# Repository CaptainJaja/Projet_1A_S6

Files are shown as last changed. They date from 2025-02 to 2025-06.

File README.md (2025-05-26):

# 🚀 Projet 1A S6 - Robot Bluetooth + Odometrie

Ce projet consiste à concevoir un robot télécommandé via Bluetooth grâce à une application Android, avec odométrie, détection d'obstacles, et supervision ROS.

---

## 📌 Cahier des charges

### 🔹 Robot
- Communication **UART** avec le module **Bluetooth HC-05**  
- **Contrôle de deux moteurs DC à encodeurs** via un driver **TB6612FNG**  
- **Lecture des encodeurs** pour faire de l'**odométrie**  
- **Connexion à une Raspberry Pi** pour supervision et traitement via **ROS**  
- **Détection d'obstacle** via un capteur **ultrason HC-SR04**  
- **Module infrarouge** pour détection de ligne ou d'obstacles courts  
- **Affichage LED** pour état du robot ou esthétique  
- **Commande de deux servo-moteurs** pour actionner des éléments  

### 🔹 Application Android
- Interface graphique avec **boutons de commande**  
- **Connexion Bluetooth** pour envoyer des commandes au robot  

---

## ⚙️ Matériel utilisé

| Composant | Référence | Rôle |
|---|---|---|
| **Microcontrôleur** | STM32 (modèle à préciser) | Gestion des moteurs, capteurs, servo et communication Bluetooth |
| **Module Bluetooth** | HC-06 / HC-05 | Communication avec l’application Android |
| **Moteurs DC à encodeur** | GA12-N20 + encodeur magnétique | Déplacement du robot + odométrie |
| **Driver moteur** | TB6612FNG | Pilotage des moteurs |
| **Batterie** | LiPo 7.4V (capacité à préciser) | Alimentation du système |
| **Régulateurs de tension** | 7.4V → 5V (R-78B5.0-2.0), 5V → 3.3V (BU33SD5WG-TR)| Alimentation des composants |
| **Capteur ultrason** | HC-SR04 | Détection d'obstacles |
| **Module infrarouge** | (modèle à préciser) | Détection de ligne ou d'obstacle proche |
| **Servomoteurs** | (modèle à préciser) x2 | Actionneurs divers |
| **LEDs** | 2x minimum | Indicateurs visuels |
| **Raspberry Pi** | (modèle à préciser) | Exécution de ROS et traitement haut niveau |

---

## 🛠 Architecture du PCB

Notre projet comporte **deux versions de PCB** :

### V1 : Prototype de base
- Connecteurs moteurs, servo, HC-SR04, HC-05 ; Driver ; STM
- Pas d'encodeur, ni module infrarouge, ni connecteurs pour la Raspberry Pi

### V2 : Version finale
- Connecteurs pour les **encodeurs**, la **Raspberry Pi**, et le **module infrarouge** ajoutés
- Circuits d'alimentation optimisés pour alimentation partagée

---

## ⏳ Tableau d'avancement du projet

| Séance | Avancement |
|---|---|
| Séance 1 | Répartition des tâches (modélisation 3D / code + PCB / appli Android), choix des composants |
| Séance 2 | - Début du PCB V1 (sans encodeur, Raspberry, infrarouge) <br>- Début application Android <br>- Début modélisation mécanique |
| Séance 3 | - Finalisation du PCB V1 <br>- 1ère version de l'application (nombreuses fonctionnalités manquantes)<br>-la conception 3D continue d'avancer |
| Séance 4 | - Début des tests du **module HC-05** <br>- Implémentation des fonctionnalités mais beaucoup d'erreurs <br>-changement des dimensions de la structure 3D car changement d'agencement des éléments dans le robot |
| Séance 5 | Finalisation de la **commande à distance** (prototype robot avec HC-05)<br>-la conception 3D continue d'avancer |
| Séance 6 | - Début du PCB V2 (ajout Raspberry, encodeurs, infrarouge) <br>- Plus d'erreurs grâce aux bonnes permissions demandées <br>- début de l'impression 3D |
| Séance 7 | Finalisation du modèle du PCB V2, **commande des composants et du PCB** <br>-fin de l'impression 3D |
| Séance 8 | Finalisation du modèle 3D, montage PCB et robot prototype, test |
| Séance 9 | Corrections et impressions 3D, montage du robot final |
---

## 📋 Répartition des tâches

| Nom | Tâche principale |
|---|---|
| **CAPODAGI Janus** | Conception PCB (https://github.com/CaptainJaja/Projet_1A_S6/tree/main/Hardware/PCB),  code STM32 (https://github.com/CaptainJaja/Projet_1A_S6/tree/main/Software/Code) |
| **BUI HAI Christophe** | Développement de l’application Android (https://github.com/CaptainJaja/Projet_1A_S6/tree/main/Application) |
| **MILLON Raphaëlle** | Conception mécanique du robot :modélisation 3D, intégration Raspberry (https://github.com/CaptainJaja/Projet_1A_S6/tree/main/Hardware/3D) |

---

## 📝 Remarques et pistes d'amélioration

- Ajouter un schéma de l'architecture du système (STM32 + Raspberry + ROS)
- Tester la communication entre STM32 et Raspberry via UART 

---

Ce README est susceptible d'être mis à jour au fur et à mesure de l'avancement du projet. 🚀

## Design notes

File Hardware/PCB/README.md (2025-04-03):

# 🚀 Robot PCB - STM32 + HC-05 + Motor Driver  

Ce projet est un PCB conçu pour contrôler un robot suiveur de ligne avec obstacle, utilisant un **STM32L552CCTx** et un module **Bluetooth HC-05** pour la communication. Il comprend un **driver moteur TB6612FNG**, plusieurs GPIO et connecteurs pour capteurs.

## 📸 Aperçu du PCB version 1 (moteur sans encodeur, pas de connexion raspberry)
### **Face Avant**
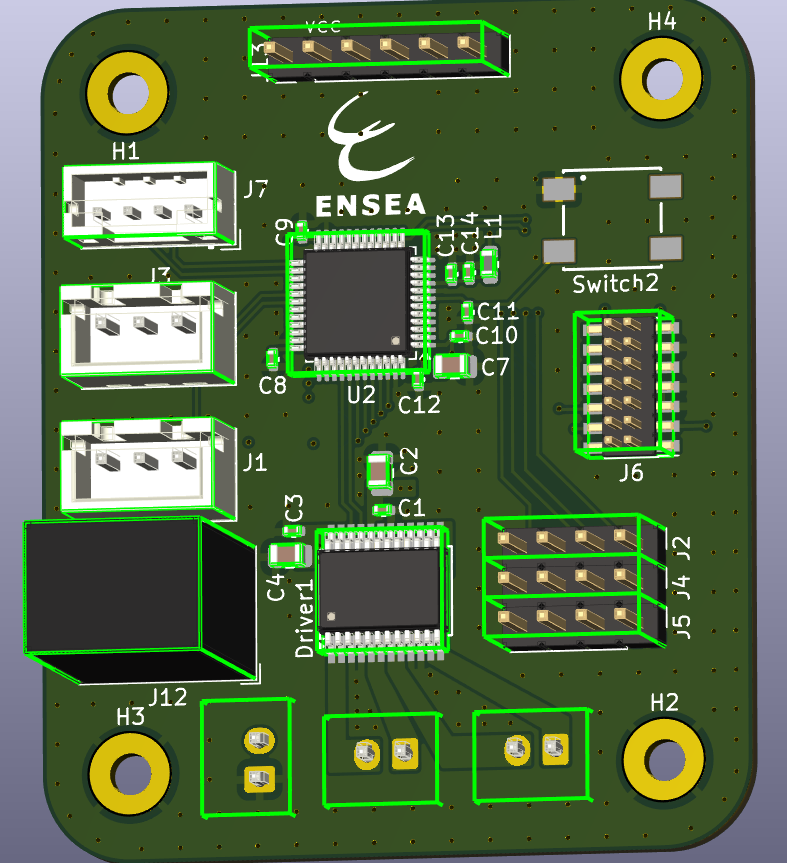
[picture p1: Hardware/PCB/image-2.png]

### **Face Arrière**
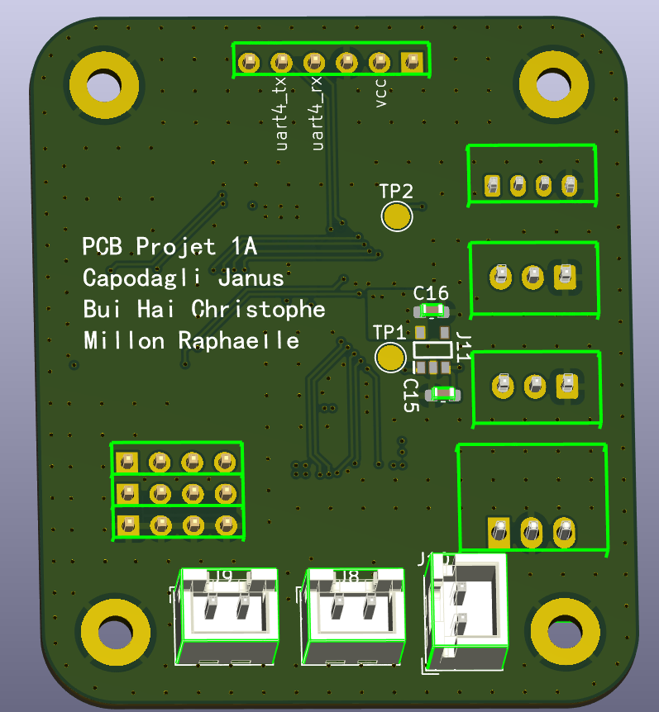
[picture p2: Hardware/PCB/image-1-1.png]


## 📸 Aperçu du PCB version 2 (+moteur avec encodeur, +connexion raspberry (UART), +Module infrarouge)
### **Face Avant**
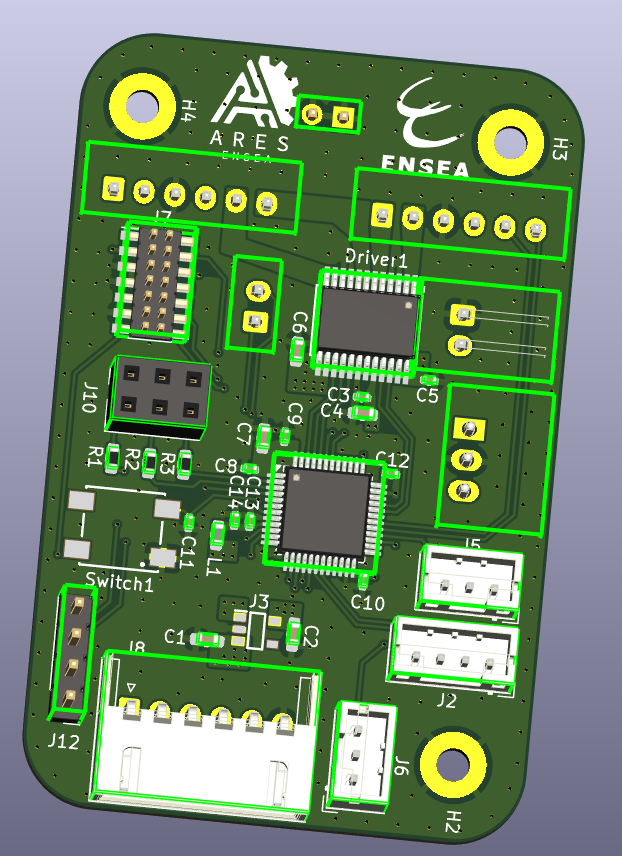
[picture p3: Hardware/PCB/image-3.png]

### **Face Arrière**
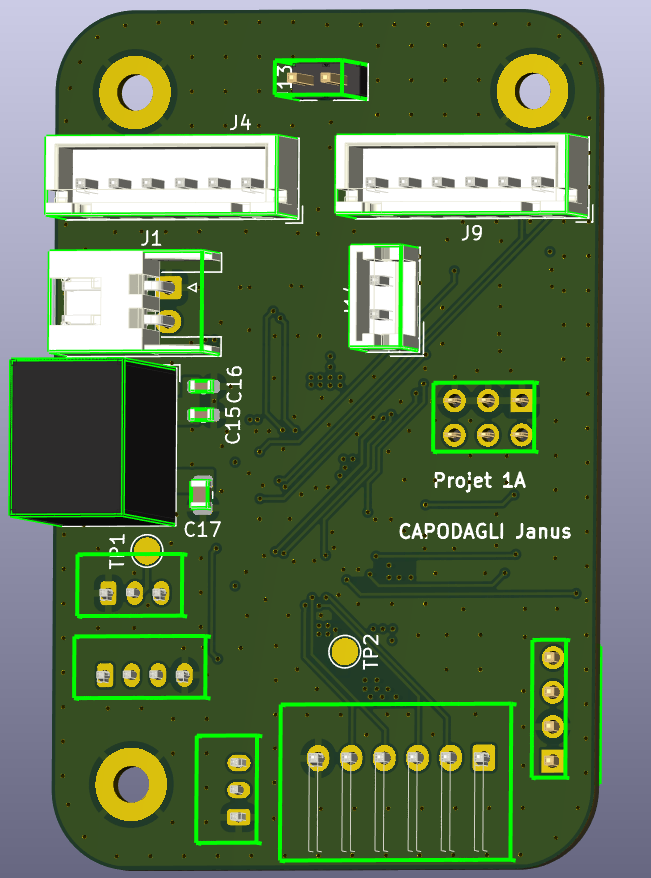
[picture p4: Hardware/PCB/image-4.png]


## 📦 Composants intégrés (version finale : V2)
- **Microcontrôleur :** STM32L552CCTx
- **Communication (PinHeader 01x04) :** HC-05 (Bluetooth, connecté en UART au MCU)
- **Contrôle des moteurs :** TB6612FNG (Driver moteur DC)
- **Indicateur d'état Bluetooth :** LED
- **Interface GPIO :** Rangée **3x4 pinheader** (GPIO-3.3V-GND)
- **Connectique :**
  - 2x **Connecteurs JST 01x03** pour servomoteurs
  - 2x **Connecteurs JST 01x06** pour moteurs DC
  - 1x **Connecteur JST 01x06** pour module infrarouge
  - 1x **Connecteur JST 01x02** pour alimentation
  - 1x **Connecteur ST-LINK** pour programmation/debug
  - 1x **Connecteur PinHeader 01x02** pour connexion UART avec raspberry
  - 1x **Connecteur PinHeader 02x03** pour connexion avec les LEDs
  - 1x **Connecteur PinHeader 01x02** pour connecter les masses STM/Raspberry
- **Alimentation :**
  - **Régulateur 7.5V → 5V**
  - **Régulateur 5V → 3.3V**
- **Boutons poussoirs :**
  - **Reset du MCU**
- **Passifs :** Condensateurs de découplage, bobine, résistances (**SMD**)

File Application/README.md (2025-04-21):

# Contrôle d'une Voiture Télécommandée via Bluetooth

## Introduction

Nous souhaitons programmer une application sur **Android Studio** afin de contrôler une voiture télécommandée via **Bluetooth** depuis un smartphone.

---

## Difficultés

- **Android Studio** utilise trois langages de programmation : **Kotlin, Java et XML**.
- Les fichiers présents sur GitHub contiennent un programme en **Kotlin** permettant d’établir une connexion Bluetooth.
- Cependant, ce programme comporte des **erreurs** que je n’arrive pas à corriger (ne connaissant pas Kotlin).
- Par conséquent, j’ai décidé de configurer **Android Studio** pour ne programmer qu’en **Java**.

---

## Mise en place du code Java

Sur un **nouveau projet vierge** :

### 1️⃣ Remplacement du fichier MainActivity
📂 **Chemin du fichier :**  
`D:\Projets\Formation_Android_Studio\app\src\main\java\com\example\formation`

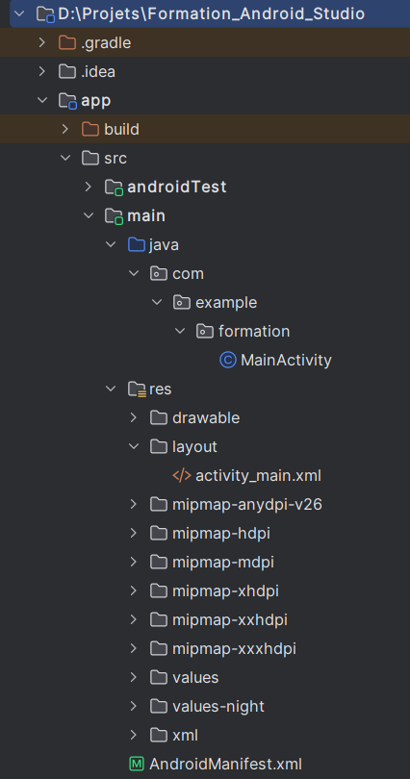
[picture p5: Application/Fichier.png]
Fichier


✅ **Modification :**  
- Remplacement du fichier **MainActivity.kt** par une classe **Java**.

### 2️⃣ Modification du fichier activity_main.xml
📂 **Chemin du fichier :**  
`D:\Projets\Formation_Android_Studio\app\src\main\res\layout\activity_main.xml`

🖼️ **Objectif :**  
- Ajuster automatiquement l’interface utilisateur aux dimensions de l’appareil.
- Le fichier `activity_main.xml` gère la **mise en page de l’application**.

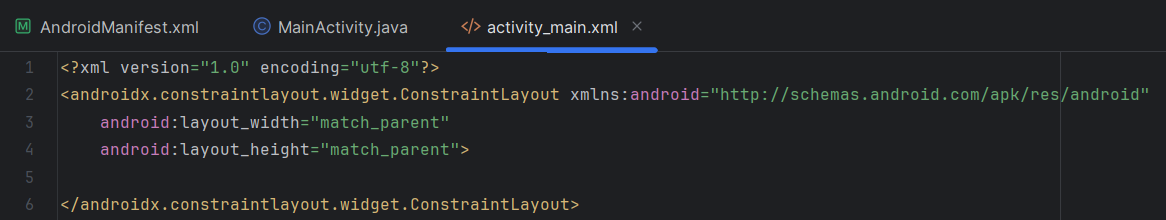
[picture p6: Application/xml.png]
activity_main.xml


### 3️⃣ Configuration du fichier AndroidManifest.xml
📂 **Chemin du fichier :**  
`D:\Projets\Formation_Android_Studio\app\src\main\AndroidManifest.xml`

✅ **Modifications :**  
- Déclaration de **MainActivity** comme **activité principale** de l’application.

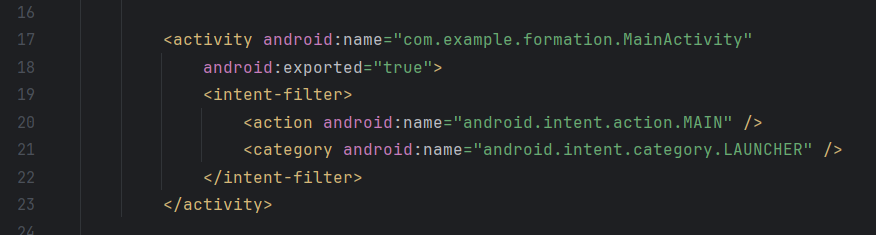
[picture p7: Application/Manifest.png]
AndroidManifest.xml


---

## Travail à faire ✅

🔹 **Se familiariser** avec **Android Studio**  
🔹 **Implémenter** le programme de **connexion Bluetooth en Java**  

---

# Séance du 06/03/2025

On en est à la version 1 du programme. Or il comporte des lacunes :

- Le programme nécessite dans le code l'adresse MAC du module Bluetooth. Dans l'idéal, on aimerait pouvoir se connecter depuis l'application à partir d'une liste d'appareils.
- Le module nécessite un PIN : le programme n'est pas adapté pour cela.
- On ne l'a pas testé car il y avait des problèmes de connexion avec le module.

On va donc en attendant essayer d'implémenter ces fonctionnalités.

---

# Séance du 13/03/2025

En modifiant le programme, j'arrive à avoir une interface sur mon portable :

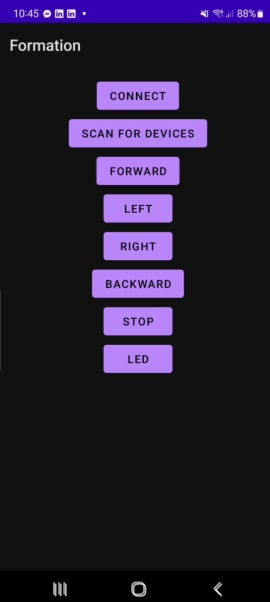
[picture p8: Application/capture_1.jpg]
Capture d'écran de l'interface


Or, à chaque fois que j'essaye de scanner les appareils environnants, l'application se ferme.  
La cause est très probablement des permissions manquantes lorsqu'on essaye d'activer le Bluetooth à partir de l'appareil.  
L'erreur non prise en compte causerait le "crash".

---

# Séance du 20/03/2025

On arrive maintenant à activer le Bluetooth à partir de l'application :

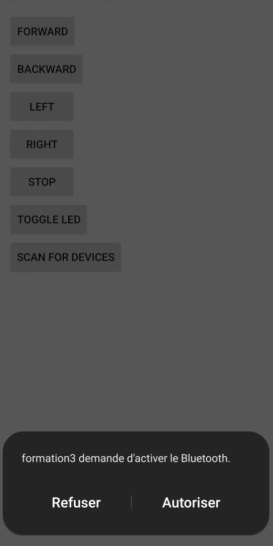
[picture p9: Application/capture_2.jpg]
Capture d'écran 2


Or, la liste d'appareils ne s'affiche toujours pas.  
Je suis incertain de la cause de l'erreur.

---

# Séance du 27/03/2025

J'ai réussi à faire en sorte que la liste s'affiche:

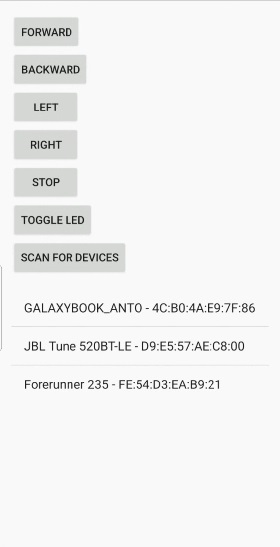
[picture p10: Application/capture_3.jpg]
Capture d'écran 3


Il fallait enfaite activer aussi la localisation de l'appareil.

---

# Séance du 27/03/2025

Maintenant Je me concentre sur le " Front End":

- J'ai modifié le l'icon de l'application avec un icon provisoire.

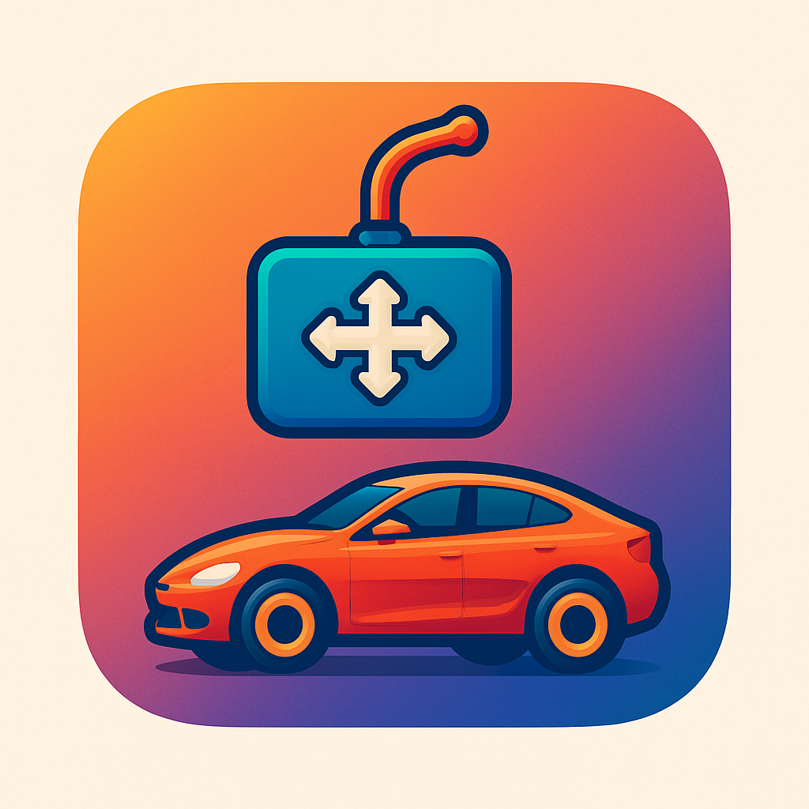
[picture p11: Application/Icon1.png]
Icon1


J'ai appris à faire des "boutons images" :

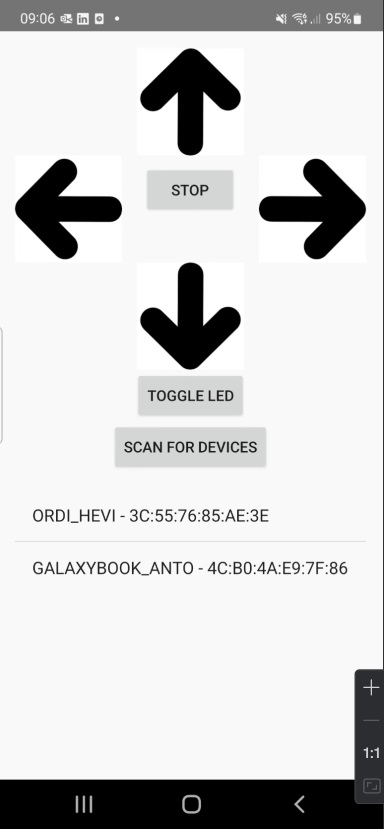
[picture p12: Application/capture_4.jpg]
Capture d'écran 4


Il ne reste plus qu'à faire des beaux sprites.

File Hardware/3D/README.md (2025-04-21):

## MODELE 3D

Voici le modèle :

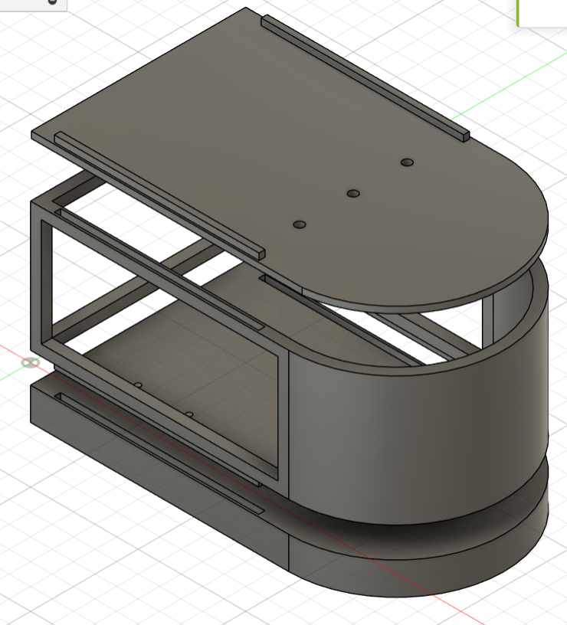
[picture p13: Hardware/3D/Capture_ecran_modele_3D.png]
Capture écran du modele 3D


Voici le rendu : 

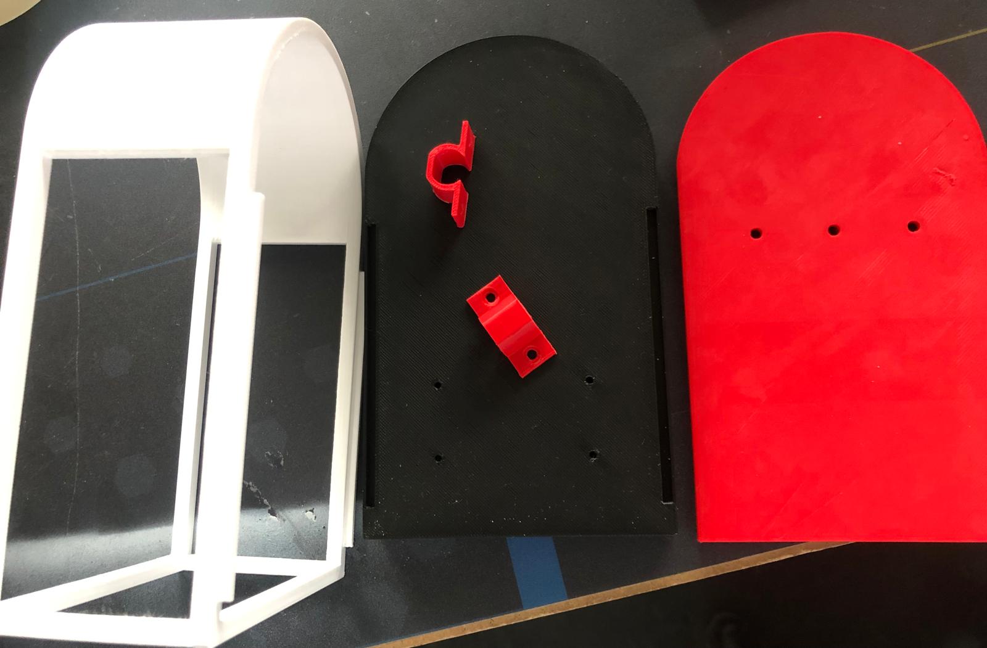
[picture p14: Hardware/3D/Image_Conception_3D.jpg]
Photo de la conception 3D


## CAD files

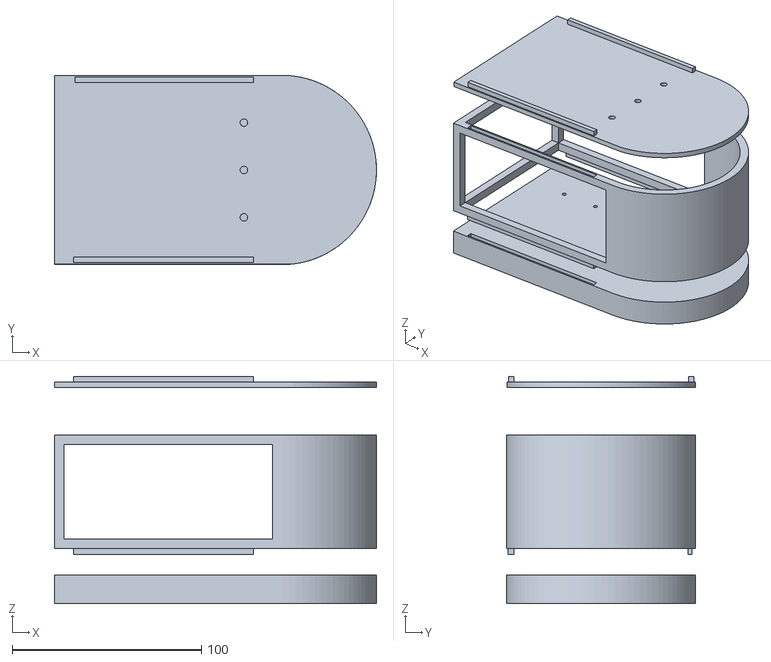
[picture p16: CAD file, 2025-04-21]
Hardware/3D/Modele3D_Projet1A.stl
170.0 x 100.0 x 120.0

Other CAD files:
Hardware/3D/Modele3D_FusionAutodesk.f3d

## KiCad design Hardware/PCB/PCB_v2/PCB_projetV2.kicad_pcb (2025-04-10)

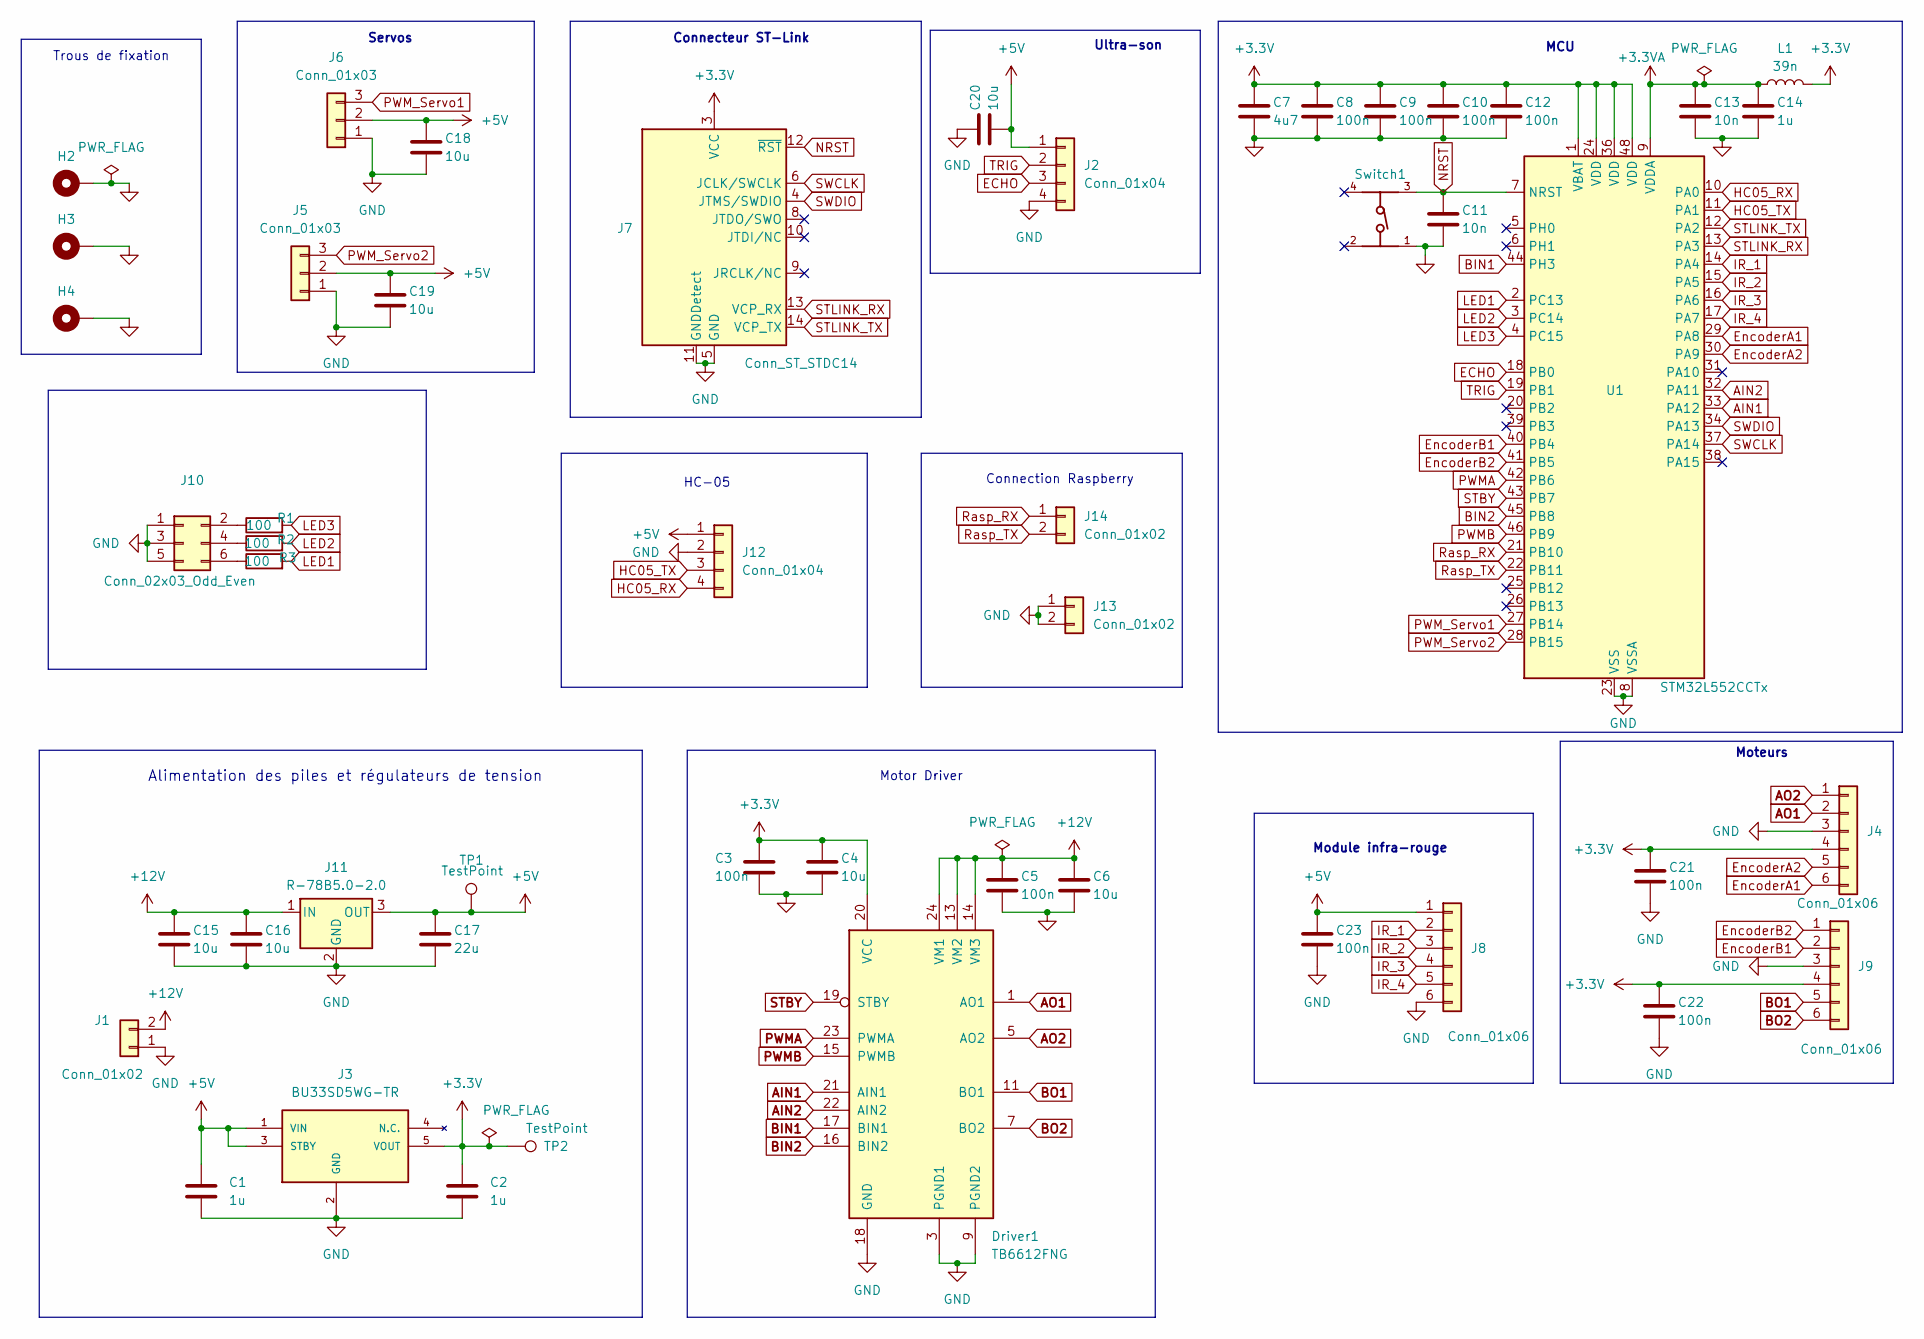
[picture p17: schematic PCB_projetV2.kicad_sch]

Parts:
C1, C2: 1u; C_0603_1608Metric_Pad1.08x0.95mm_HandSolder
C3, C5, C8, C9, C10, C12, C21, C22, C23: 100n; C_0402_1005Metric
C4, C6, C15, C16, C18, C19, C20: 10u; C_0603_1608Metric
C7: 4u7; C_0603_1608Metric
C11, C13: 10n; C_0402_1005Metric
C14: 1u; C_0402_1005Metric
C17: 22u; C_0805_2012Metric
Driver1: TB6612FNG; SSOP-24_5.3x8.2mm_P0.65mm
H2, H3, H4: MountingHole_Pad; MountingHole_2.7mm_M2.5_Pad
J1: Conn_01x02; JST_XH_S2B-XH-A-1_1x02_P2.50mm_Horizontal
J2: Conn_01x04; JST_PH_B4B-PH-K_1x04_P2.00mm_Vertical
J3: BU33SD5WG-TR; SOT95P280X125-5N; Mouser_Part_Number 755-BU33SD5WG-TR
J4, J9: Conn_01x06; JST_XH_B6B-XH-A_1x06_P2.50mm_Vertical
J5, J6: Conn_01x03; JST_PH_B3B-PH-K_1x03_P2.00mm_Vertical
J7: Conn_ST_STDC14; PinHeader_2x07_P1.27mm_Vertical_SMD
J8: Conn_01x06; JST_XH_S6B-XH-A-1_1x06_P2.50mm_Horizontal
J10: Conn_02x03_Odd_Even; PinSocket_2x03_P2.54mm_Vertical
J11: R-78B5.0-2.0; Converter_DCDC_RECOM_R-78B-2.0_THT
J12: Conn_01x04; PinHeader_1x04_P2.54mm_Vertical
J13: Conn_01x02; PinHeader_1x02_P2.54mm_Vertical
J14: Conn_01x02; JST_EH_B2B-EH-A_1x02_P2.50mm_Vertical
L1: 39n; L_0603_1608Metric
R1, R2, R3: 100; R_0603_1608Metric
Switch1: 430471025826; PART-NUMBER 430471025826
TP1, TP2: TestPoint; TestPoint_Pad_D2.0mm
U1: STM32L552CCTx; LQFP-48_7x7mm_P0.5mm

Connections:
+3.3V: C2.1, C3.1, C4.1, C7.1, C8.1, C9.1, C10.1, C12.1, C21.1, C22.1, Driver1.20 (VCC), J3.5 (VOUT), J4.4, J7.3 (VCC), J9.4, L1.2, TP2.1, U1.1 (VBAT), U1.24 (VDD), U1.36 (VDD), U1.48 (VDD)
+3.3VA: C13.1, C14.1, L1.1, U1.9 (VDDA)
+5V: C1.1, C17.1, C18.1, C19.1, C20.2, C23.1, J2.1, J3.1 (VIN), J3.3 (STBY), J5.2, J6.2, J8.1, J11.3 (OUT), J12.1, TP1.1
+12V: C5.1, C6.1, C15.1, C16.1, Driver1.13 (VM2), Driver1.14 (VM3), Driver1.24 (VM1), J1.2, J11.1 (IN)
AIN1: Driver1.21 (AIN1), U1.33 (PA12)
AIN2: Driver1.22 (AIN2), U1.32 (PA11)
AO1: Driver1.1 (AO1), Driver1.2 (AO1), J4.2
AO2: Driver1.5 (AO2), Driver1.6 (AO2), J4.1
BIN1: Driver1.17 (BIN1), U1.44 (PH3)
BIN2: Driver1.16 (BIN2), U1.45 (PB8)
BO1: Driver1.11 (BO1), Driver1.12 (BO1), J9.5
BO2: Driver1.7 (BO2), Driver1.8 (BO2), J9.6
ECHO: J2.3, U1.18 (PB0)
EncoderA1: J4.6, U1.29 (PA8)
EncoderA2: J4.5, U1.30 (PA9)
EncoderB1: J9.2, U1.40 (PB4)
EncoderB2: J9.1, U1.41 (PB5)
GND: C1.2, C2.2, C3.2, C4.2, C5.2, C6.2, C7.2, C8.2, C9.2, C10.2, C11.2, C12.2, C13.2, C14.2, C15.2, C16.2, C17.2, C18.2, C19.2, C20.1, C21.2, C22.2, C23.2, Driver1.3 (PGND1), Driver1.4 (PGND1), Driver1.9 (PGND2), Driver1.10 (PGND2), Driver1.18 (GND), H2.1, H3.1, H4.1, J1.1, J2.4, J3.2 (GND), J4.3, J5.1, J6.1, J7.5 (GND), J7.7 (GND), J7.11 (GNDDetect), J8.6, J9.3, J10.1, J10.3, J10.5, J11.2 (GND), J12.2, J13.1, J13.2, Switch1.1, U1.8 (VSSA), U1.23 (VSS), U1.35 (VSS), U1.47 (VSS)
HC05_RX: J12.4, U1.10 (PA0)
HC05_TX: J12.3, U1.11 (PA1)
IR_1: J8.2, U1.14 (PA4)
IR_2: J8.3, U1.15 (PA5)
IR_3: J8.4, U1.16 (PA6)
IR_4: J8.5, U1.17 (PA7)
LED1: R3.2, U1.2 (PC13)
LED2: R2.2, U1.3 (PC14)
LED3: R1.2, U1.4 (PC15)
NRST: C11.1, J7.12 (~RST), Switch1.3, U1.7 (NRST)
unnamed: J10.2, R1.1
unnamed: J10.4, R2.1
unnamed: J10.6, R3.1
PWMA: Driver1.23 (PWMA), U1.42 (PB6)
PWMB: Driver1.15 (PWMB), U1.46 (PB9)
PWM_Servo1: J6.3, U1.27 (PB14)
PWM_Servo2: J5.3, U1.28 (PB15)
Rasp_RX: J14.1, U1.21 (PB10)
Rasp_TX: J14.2, U1.22 (PB11)
STBY: Driver1.19 (STBY), U1.43 (PB7)
STLINK_RX: J7.13 (VCP_RX), U1.13 (PA3)
STLINK_TX: J7.14 (VCP_TX), U1.12 (PA2)
SWCLK: J7.6 (JCLK/SWCLK), U1.37 (PA14)
SWDIO: J7.4 (JTMS/SWDIO), U1.34 (PA13)
TRIG: J2.2, U1.19 (PB1)

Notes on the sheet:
Module infra-rouge
Alimentation des piles et régulateurs de tension
Trous de fixation
Connection Raspberry
HC-05
Moteurs
Servos
Motor Driver
MCU
Ultra-son
Connecteur ST-Link

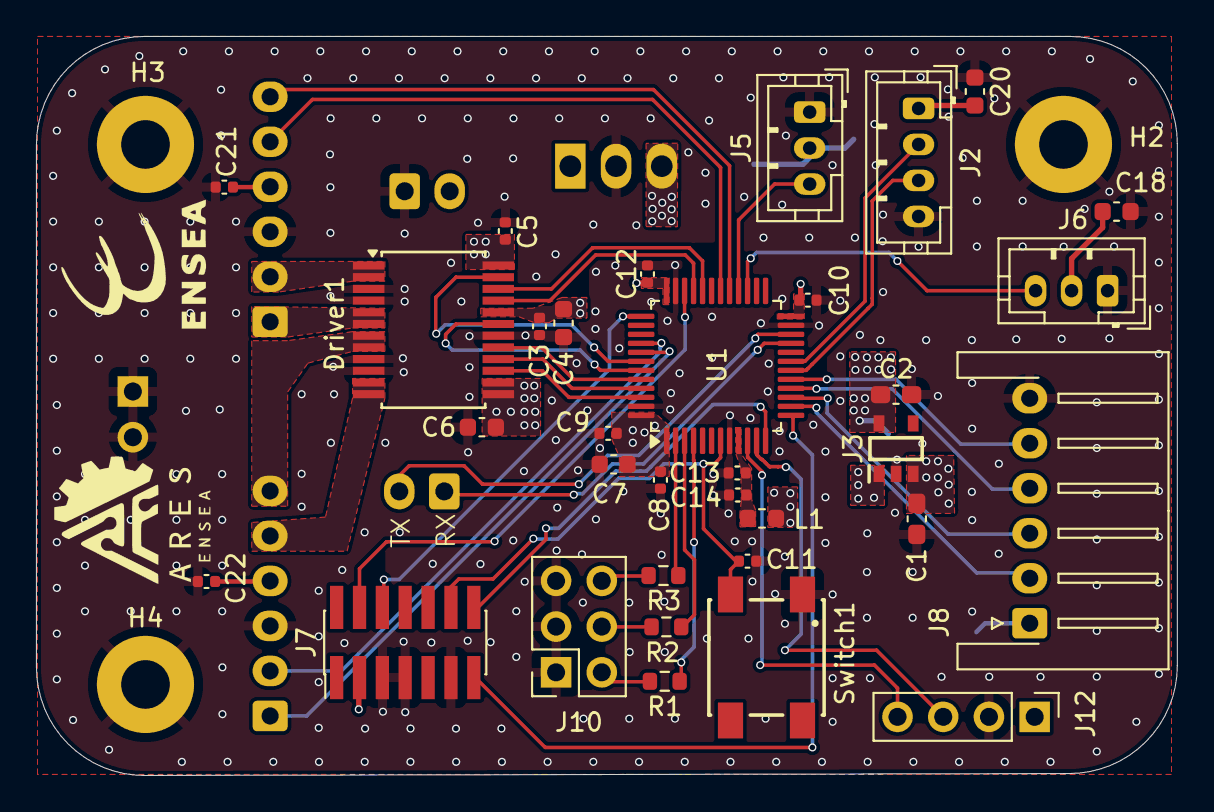
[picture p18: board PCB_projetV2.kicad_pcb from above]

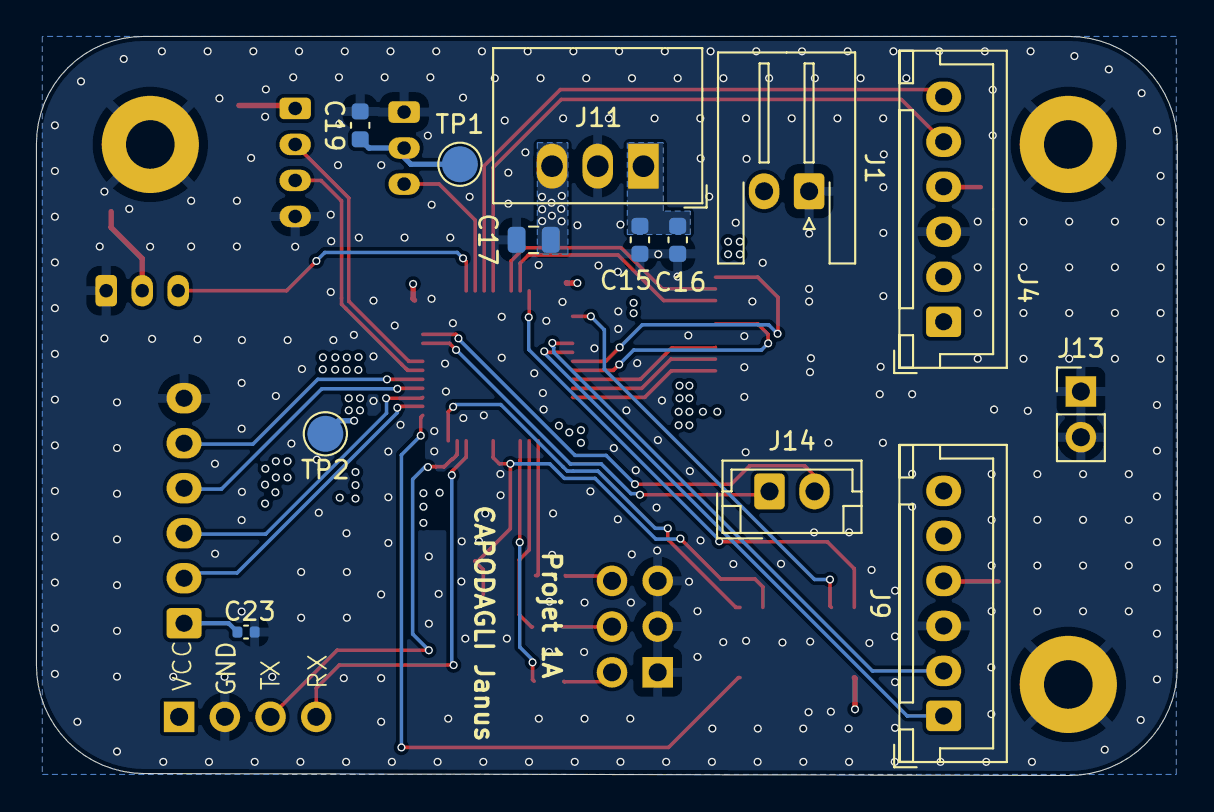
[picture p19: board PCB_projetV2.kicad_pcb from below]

Board: 4 copper layers, 63.4 x 41.1 mm, 49 parts (13 on the bottom side), 43 nets.

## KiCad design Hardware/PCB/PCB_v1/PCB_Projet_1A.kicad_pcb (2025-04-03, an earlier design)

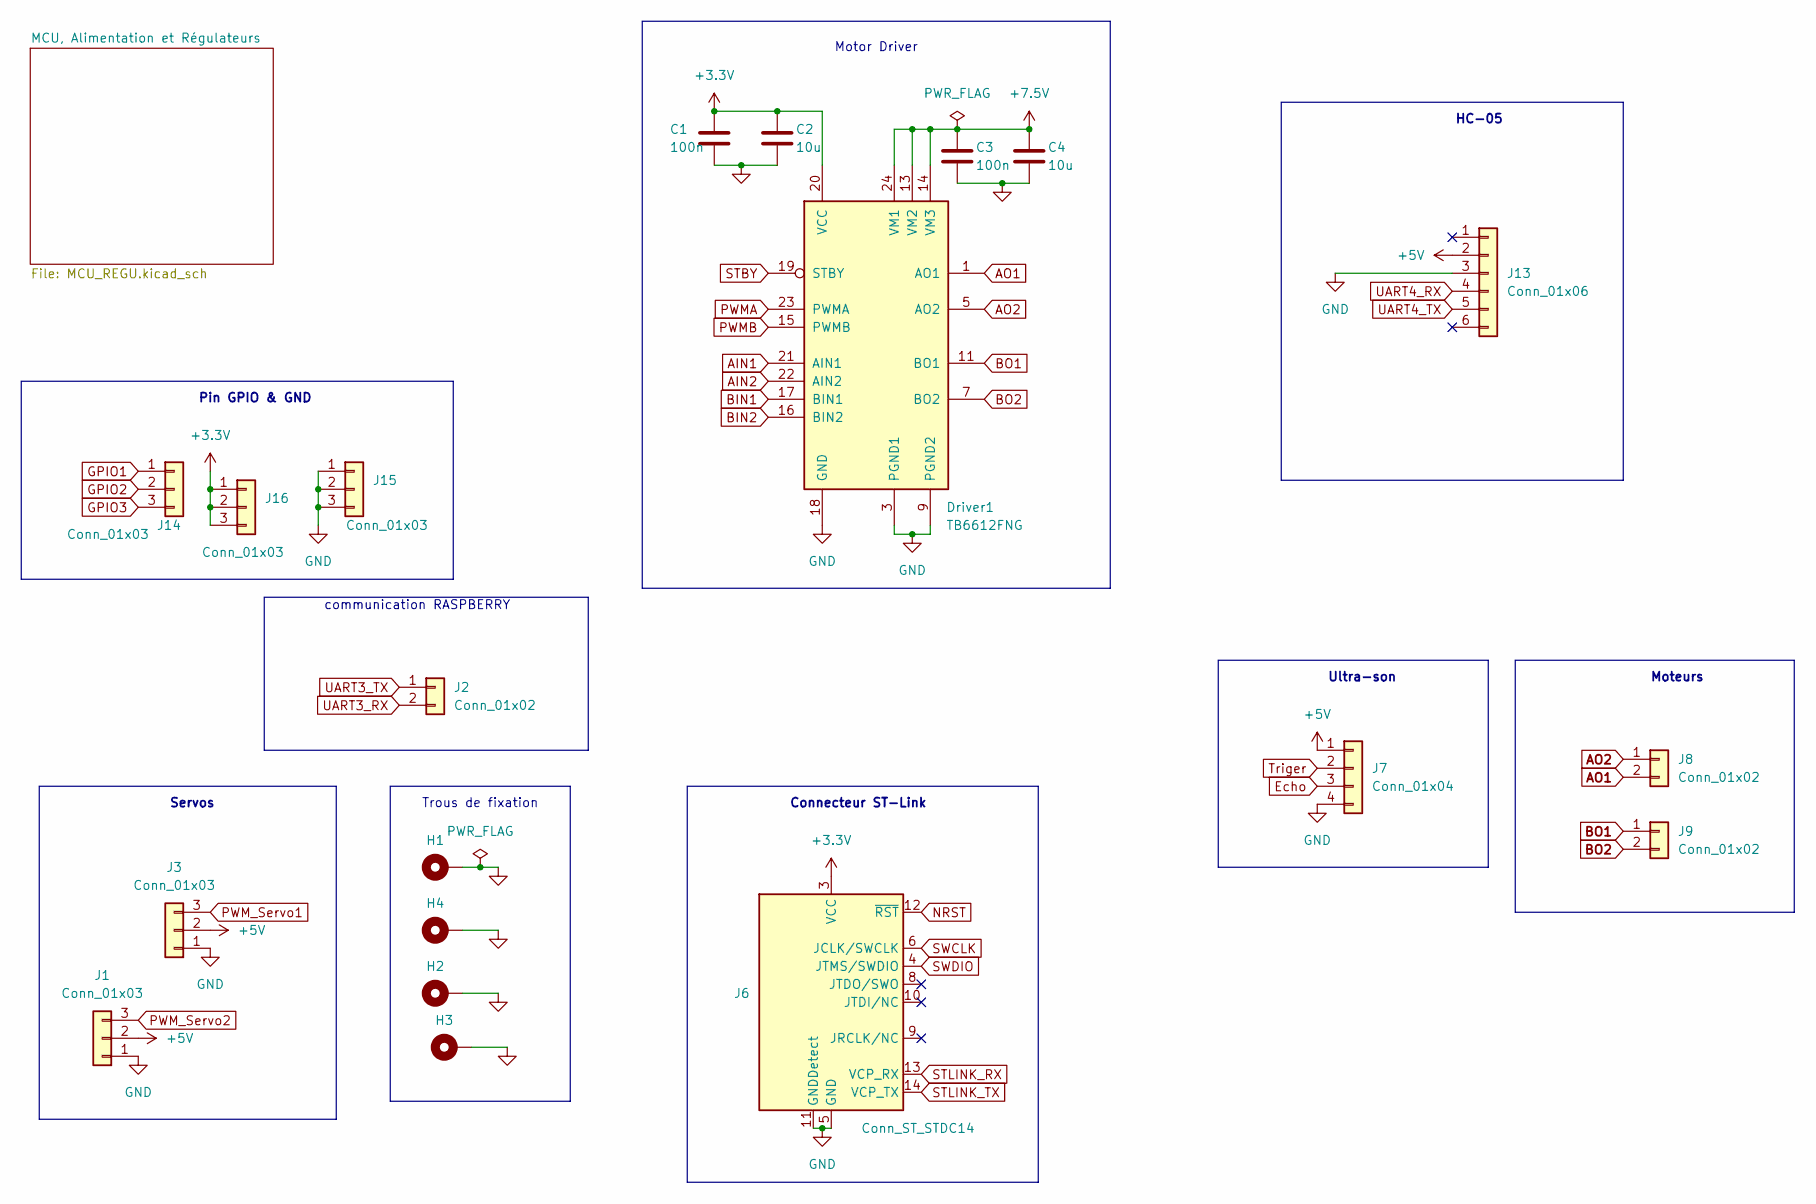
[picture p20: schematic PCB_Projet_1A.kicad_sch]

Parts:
C1, C3: 100n; C_0402_1005Metric
C2, C4: 10u; C_0805_2012Metric
Driver1: TB6612FNG; SSOP-24_5.3x8.2mm_P0.65mm
H1, H2, H3, H4: MountingHole_Pad; MountingHole_2.7mm_M2.5_Pad
J1, J3: Conn_01x03; JST_XH_B3B-XH-A_1x03_P2.50mm_Vertical
J2: Conn_01x02; PinHeader_1x02_P2.54mm_Horizontal
J6: Conn_ST_STDC14; PinHeader_2x07_P1.27mm_Vertical_SMD
J7: Conn_01x04; JST_PH_B4B-PH-K_1x04_P2.00mm_Vertical
J8, J9: Conn_01x02; JST_XH_B2B-XH-A_1x02_P2.50mm_Vertical
J13: Conn_01x06; PinHeader_1x06_P2.54mm_Vertical
J14, J15, J16: Conn_01x03; PinHeader_1x03_P2.54mm_Vertical

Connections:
+3.3V: C1.1, C2.1, Driver1.20 (VCC), J6.3 (VCC), J16.1, J16.2, J16.3; also elsewhere on the board
+5V: J1.2, J3.2, J7.1, J13.2; also elsewhere on the board
+7.5V: C3.1, C4.1, Driver1.13 (VM2), Driver1.14 (VM3), Driver1.24 (VM1); also elsewhere on the board
AIN1: Driver1.21 (AIN1); also elsewhere on the board
AIN2: Driver1.22 (AIN2); also elsewhere on the board
AO1: Driver1.1 (AO1), Driver1.2 (AO1), J8.2
AO2: Driver1.5 (AO2), Driver1.6 (AO2), J8.1
BIN1: Driver1.17 (BIN1); also elsewhere on the board
BIN2: Driver1.16 (BIN2); also elsewhere on the board
BO1: Driver1.11 (BO1), Driver1.12 (BO1), J9.1
BO2: Driver1.7 (BO2), Driver1.8 (BO2), J9.2
Echo: J7.3; also elsewhere on the board
GND: C1.2, C2.2, C3.2, C4.2, Driver1.3 (PGND1), Driver1.4 (PGND1), Driver1.9 (PGND2), Driver1.10 (PGND2), Driver1.18 (GND), H1.1, H2.1, H3.1, H4.1, J1.1, J3.1, J6.5 (GND), J6.7 (GND), J6.11 (GNDDetect), J7.4, J13.3, J15.1, J15.2, J15.3; also elsewhere on the board
GPIO1: J14.1; also elsewhere on the board
GPIO2: J14.2; also elsewhere on the board
GPIO3: J14.3; also elsewhere on the board
NRST: J6.12 (~RST)
PWMA: Driver1.23 (PWMA); also elsewhere on the board
PWMB: Driver1.15 (PWMB); also elsewhere on the board
PWM_Servo1: J3.3; also elsewhere on the board
PWM_Servo2: J1.3; also elsewhere on the board
STBY: Driver1.19 (STBY); also elsewhere on the board
STLINK_RX: J6.13 (VCP_RX); also elsewhere on the board
STLINK_TX: J6.14 (VCP_TX); also elsewhere on the board
SWCLK: J6.6 (JCLK/SWCLK); also elsewhere on the board
SWDIO: J6.4 (JTMS/SWDIO); also elsewhere on the board
Triger: J7.2; also elsewhere on the board
UART3_RX: J2.2; also elsewhere on the board
UART3_TX: J2.1; also elsewhere on the board
UART4_RX: J13.4; also elsewhere on the board
UART4_TX: J13.5; also elsewhere on the board

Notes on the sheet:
Ultra-son
Servos
communication RASPBERRY
Connecteur ST-Link
Trous de fixation
Moteurs
Pin GPIO & GND
HC-05
Motor Driver

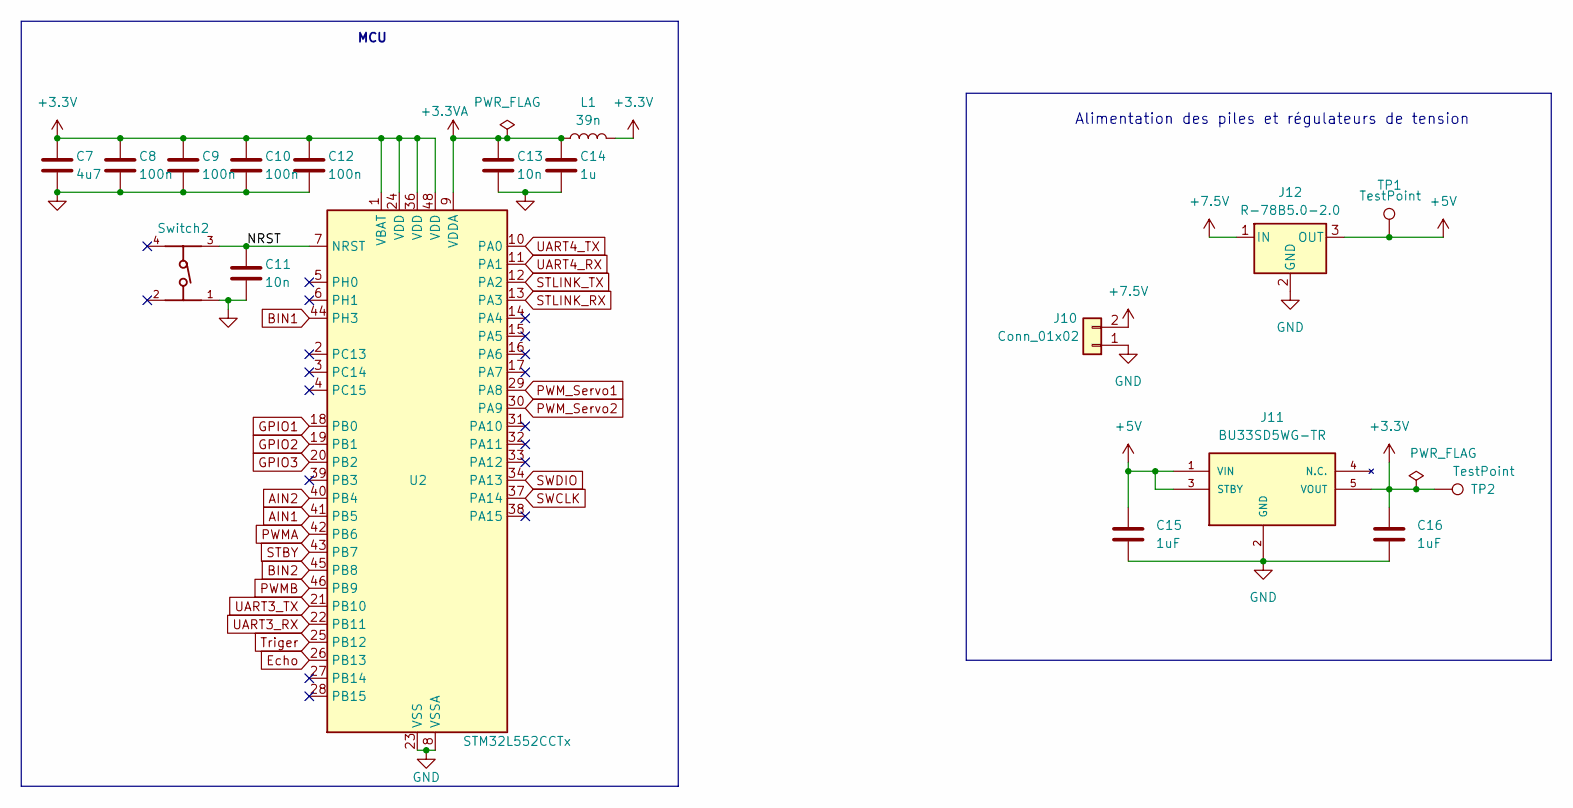
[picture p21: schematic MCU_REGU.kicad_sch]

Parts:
C7: 4u7; C_0805_2012Metric
C8, C9, C10, C12: 100n; C_0402_1005Metric
C11, C13: 10n; C_0402_1005Metric
C14: 1u; C_0402_1005Metric
C15, C16: 1uF; C_0603_1608Metric_Pad1.08x0.95mm_HandSolder
J10: Conn_01x02; JST_XH_B2B-XH-A_1x02_P2.50mm_Vertical
J11: BU33SD5WG-TR; SOT95P280X125-5N; Mouser_Part_Number 755-BU33SD5WG-TR
J12: R-78B5.0-2.0; Converter_DCDC_RECOM_R-78B-2.0_THT
L1: 39n; L_0603_1608Metric
Switch2: 430471025826; PART-NUMBER 430471025826
TP1, TP2: TestPoint; TestPoint_Pad_D2.0mm
U2: STM32L552CCTx; LQFP-48_7x7mm_P0.5mm

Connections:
+3.3V: C7.1, C8.1, C9.1, C10.1, C12.1, C16.1, J11.5 (VOUT), L1.2, TP2.1, U2.1 (VBAT), U2.24 (VDD), U2.36 (VDD), U2.48 (VDD); also elsewhere on the board
+3.3VA: C13.1, C14.1, L1.1, U2.9 (VDDA)
+5V: C15.1, J11.1 (VIN), J11.3 (STBY), J12.3 (OUT), TP1.1; also elsewhere on the board
+7.5V: J10.2, J12.1 (IN); also elsewhere on the board
/MCU, Alimentation et Régulateurs/NRST: C11.1, Switch2.3, U2.7 (NRST)
AIN1: U2.41 (PB5); also elsewhere on the board
AIN2: U2.40 (PB4); also elsewhere on the board
BIN1: U2.44 (PH3); also elsewhere on the board
BIN2: U2.45 (PB8); also elsewhere on the board
Echo: U2.26 (PB13); also elsewhere on the board
GND: C7.2, C8.2, C9.2, C10.2, C11.2, C12.2, C13.2, C14.2, C15.2, C16.2, J10.1, J11.2 (GND), J12.2 (GND), Switch2.1, U2.8 (VSSA), U2.23 (VSS), U2.35 (VSS), U2.47 (VSS); also elsewhere on the board
GPIO1: U2.18 (PB0); also elsewhere on the board
GPIO2: U2.19 (PB1); also elsewhere on the board
GPIO3: U2.20 (PB2); also elsewhere on the board
PWMA: U2.42 (PB6); also elsewhere on the board
PWMB: U2.46 (PB9); also elsewhere on the board
PWM_Servo1: U2.29 (PA8); also elsewhere on the board
PWM_Servo2: U2.30 (PA9); also elsewhere on the board
STBY: U2.43 (PB7); also elsewhere on the board
STLINK_RX: U2.13 (PA3); also elsewhere on the board
STLINK_TX: U2.12 (PA2); also elsewhere on the board
SWCLK: U2.37 (PA14); also elsewhere on the board
SWDIO: U2.34 (PA13); also elsewhere on the board
Triger: U2.25 (PB12); also elsewhere on the board
UART3_RX: U2.22 (PB11); also elsewhere on the board
UART3_TX: U2.21 (PB10); also elsewhere on the board
UART4_RX: U2.11 (PA1); also elsewhere on the board
UART4_TX: U2.10 (PA0); also elsewhere on the board

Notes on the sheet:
MCU
Alimentation des piles et régulateurs de tension

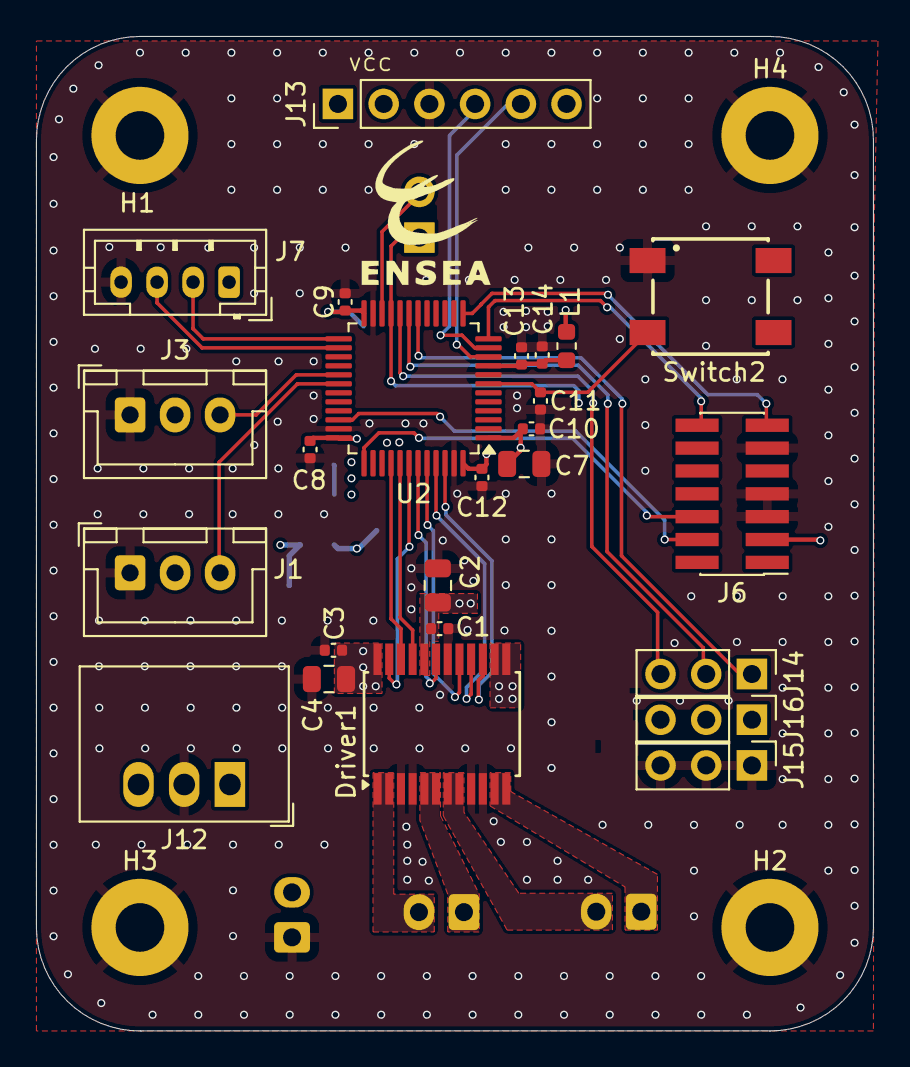
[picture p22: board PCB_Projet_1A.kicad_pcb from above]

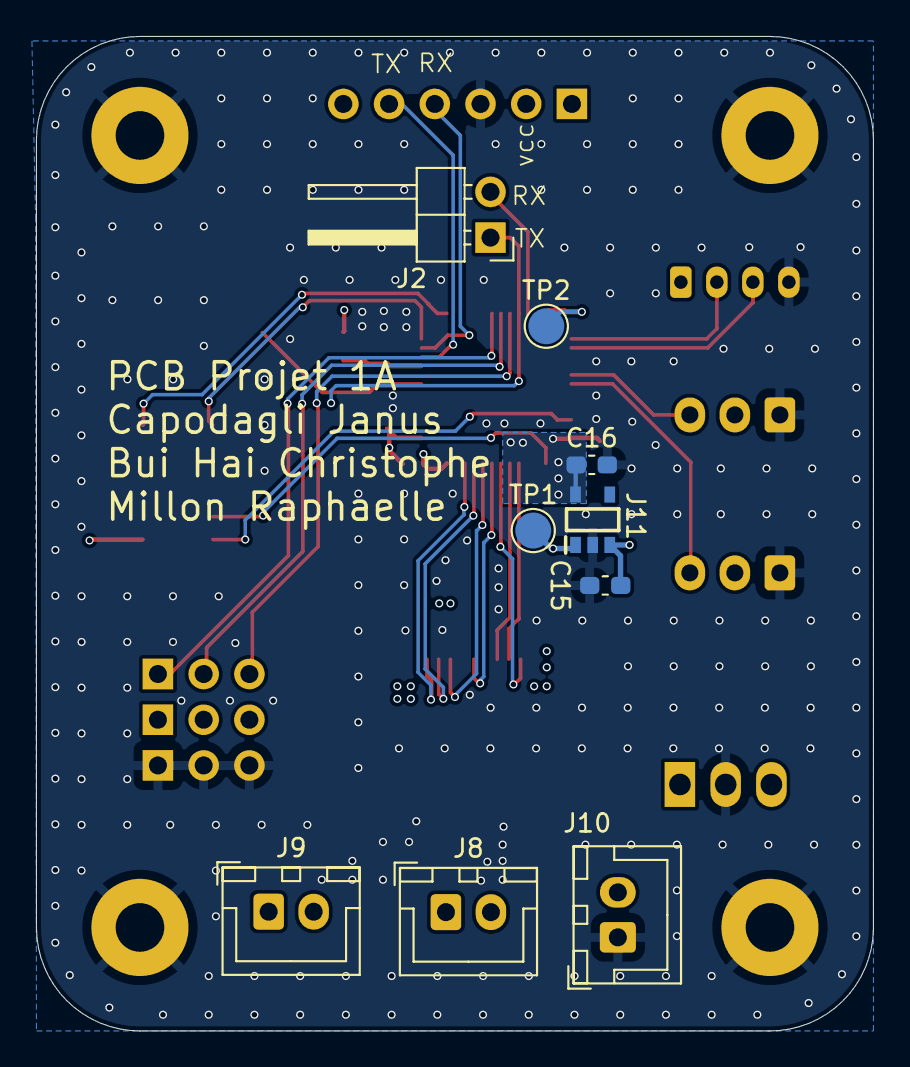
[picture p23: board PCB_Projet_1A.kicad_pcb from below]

Board: 4 copper layers, 46.5 x 55.2 mm, 38 parts (9 on the bottom side), 32 nets.

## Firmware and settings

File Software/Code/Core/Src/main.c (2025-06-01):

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
/* Includes ------------------------------------------------------------------*/
#include "main.h"

/* USER CODE BEGIN Includes */
#include <stdio.h>
#include <string.h>
#include "Functions.h"
/* USER CODE END Includes */

/* USER CODE BEGIN PD */
#define BUFFER_SIZE 1



#define LED_BLUE_PIN GPIO_PIN_15
#define LED_BLUE_PORT GPIOA
/* USER CODE END PD */

ADC_HandleTypeDef hadc1;
DMA_HandleTypeDef hdma_adc1;

TIM_HandleTypeDef htim1;
TIM_HandleTypeDef htim3;
TIM_HandleTypeDef htim4;
TIM_HandleTypeDef htim15;

UART_HandleTypeDef huart4;
UART_HandleTypeDef huart2;
UART_HandleTypeDef huart3;

/* USER CODE BEGIN PV */
uint8_t received_data;

/* USER CODE END PV */

void SystemClock_Config(void);
static void MX_GPIO_Init(void);
static void MX_DMA_Init(void);
static void MX_USART2_UART_Init(void);
static void MX_TIM1_Init(void);
static void MX_UART4_Init(void);
static void MX_ADC1_Init(void);
static void MX_ICACHE_Init(void);
static void MX_TIM4_Init(void);
static void MX_TIM3_Init(void);
static void MX_TIM15_Init(void);
static void MX_USART3_UART_Init(void);
/* USER CODE BEGIN 0 */
int _write(int file, char *ptr, int len)
{
    HAL_UART_Transmit(&huart2, (uint8_t*)ptr, len, HAL_MAX_DELAY);
    return len;
}

void HAL_UART_RxCpltCallback(UART_HandleTypeDef *huart) {
    if (huart->Instance == UART4) {
    	LEDshow();
        printf("Commande reçue : %c\r\n", received_data);  // Affichage de la réception

        switch (received_data) {
            case 'z': Motor_Forward(); printf("Avance\n"); break;
            case 's': Motor_Backward(); printf("Recule\n"); break;
            case 'q': Motor_Left(); printf("Gauche\n"); break;
            case 'd': Motor_Right(); printf("Droite\n"); break;
            case ' ': Motor_Stop(); printf("Stop\n"); break;
            case 't': ToggleSpeed(); printf("ToggledSpeed\n"); break;
            default: printf("Commande inconnue\n"); break;
        }

        HAL_UART_Receive_IT(&huart4, &received_data, 1);
    }
}



/* USER CODE END 0 */

/**
  * @brief  The application entry point.
  * @retval int
  */
int main(void)
{

  /* MCU Configuration--------------------------------------------------------*/

  /* Reset of all peripherals, Initializes the Flash interface and the Systick. */
  HAL_Init();

  /* Configure the system clock */
  SystemClock_Config();

  /* Initialize all configured peripherals */
  MX_GPIO_Init();
  MX_DMA_Init();
  MX_USART2_UART_Init();
  MX_TIM1_Init();
  MX_UART4_Init();
  MX_ADC1_Init();
  MX_ICACHE_Init();
  MX_TIM4_Init();
  MX_TIM3_Init();
  MX_TIM15_Init();
  MX_USART3_UART_Init();
  /* USER CODE BEGIN 2 */
  HAL_GPIO_WritePin(STBY_GPIO_Port, STBY_Pin, 1);
  // For the motors
  HAL_TIM_PWM_Start(&htim4, TIM_CHANNEL_1);
  HAL_TIM_PWM_Start(&htim4, TIM_CHANNEL_4);
  HAL_UART_Receive_IT(&huart4, &received_data, 1);
  /* USER CODE END 2 */

  /* Infinite loop */
  /* USER CODE BEGIN WHILE */
  while (1)
  {
	 // HAL_Delay(100);
    /* USER CODE END WHILE */

    /* USER CODE BEGIN 3 */
  }
  /* USER CODE END 3 */
}

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


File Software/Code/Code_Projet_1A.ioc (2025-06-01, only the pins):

Mcu.UserName=STM32L552CCTx
PA0.GPIO_Label=HC05_RX
PA0.Signal=UART4_TX
PA1.GPIO_Label=HC05_TX
PA1.Signal=UART4_RX
PA11.GPIO_Label=AIN2
PA11.Signal=GPIO_Output
PA12.GPIO_Label=AIN1
PA12.Signal=GPIO_Output
PA2.Signal=USART2_TX
PA3.Signal=USART2_RX
PA4.GPIO_Label=X1
PA4.Signal=ADCx_IN9
PA5.GPIO_Label=X2
PA5.Signal=ADCx_IN10
PA6.GPIO_Label=X3
PA6.Signal=ADCx_IN11
PA7.GPIO_Label=X4
PA7.Signal=ADCx_IN12
PA8.GPIO_Label=EncodeurA1
PA8.Signal=S_TIM1_CH1
PA9.GPIO_Label=EncodeurA2
PA9.Signal=S_TIM1_CH2
PB0.GPIO_Label=ECHO
PB0.Signal=GPXTI0
PB1.GPIO_Label=TRIG
PB1.Signal=GPIO_Output
PB10.GPIO_Label=Raspb_RX
PB10.Signal=USART3_TX
PB11.GPIO_Label=Raspb_TX
PB11.Signal=USART3_RX
PB14.GPIO_Label=Servo1
PB14.Signal=S_TIM15_CH1
PB15.GPIO_Label=Servo2
PB15.Signal=S_TIM15_CH2
PB5.GPIO_Label=EncodeurB2
PB5.Signal=S_TIM3_CH2
PB6.GPIO_Label=PWMA
PB6.Signal=S_TIM4_CH1
PB7.GPIO_Label=STBY
PB7.Signal=GPIO_Output
PB8.GPIO_Label=BIN2
PB8.Signal=GPIO_Output
PB9.GPIO_Label=PWMB
PB9.Signal=S_TIM4_CH4
PC13.GPIO_Label=LED1
PC13.Signal=GPIO_Output
PH3-BOOT0.GPIO_Label=BIN1
PH3-BOOT0.Signal=GPIO_Output

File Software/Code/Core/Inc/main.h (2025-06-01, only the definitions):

#define LED1_Pin GPIO_PIN_13
#define LED1_GPIO_Port GPIOC
#define LED2_Pin GPIO_PIN_14
#define LED2_GPIO_Port GPIOC
#define LED3_Pin GPIO_PIN_15
#define LED3_GPIO_Port GPIOC
#define HC05_RX_Pin GPIO_PIN_0
#define HC05_RX_GPIO_Port GPIOA
#define HC05_TX_Pin GPIO_PIN_1
#define HC05_TX_GPIO_Port GPIOA
#define X1_Pin GPIO_PIN_4
#define X1_GPIO_Port GPIOA
#define X2_Pin GPIO_PIN_5
#define X2_GPIO_Port GPIOA
#define X3_Pin GPIO_PIN_6
#define X3_GPIO_Port GPIOA
#define X4_Pin GPIO_PIN_7
#define X4_GPIO_Port GPIOA
#define ECHO_Pin GPIO_PIN_0
#define ECHO_GPIO_Port GPIOB
#define TRIG_Pin GPIO_PIN_1
#define TRIG_GPIO_Port GPIOB
#define Raspb_RX_Pin GPIO_PIN_10
#define Raspb_RX_GPIO_Port GPIOB
#define Raspb_TX_Pin GPIO_PIN_11
#define Raspb_TX_GPIO_Port GPIOB
#define Servo1_Pin GPIO_PIN_14
#define Servo1_GPIO_Port GPIOB
#define Servo2_Pin GPIO_PIN_15
#define Servo2_GPIO_Port GPIOB
#define EncodeurA1_Pin GPIO_PIN_8
#define EncodeurA1_GPIO_Port GPIOA
#define EncodeurA2_Pin GPIO_PIN_9
#define EncodeurA2_GPIO_Port GPIOA
#define AIN2_Pin GPIO_PIN_11
#define AIN2_GPIO_Port GPIOA
#define AIN1_Pin GPIO_PIN_12
#define AIN1_GPIO_Port GPIOA
#define EncodeurB1_Pin GPIO_PIN_4
#define EncodeurB1_GPIO_Port GPIOB
#define EncodeurB2_Pin GPIO_PIN_5
#define EncodeurB2_GPIO_Port GPIOB
#define PWMA_Pin GPIO_PIN_6
#define PWMA_GPIO_Port GPIOB
#define STBY_Pin GPIO_PIN_7
#define STBY_GPIO_Port GPIOB
#define BIN1_Pin GPIO_PIN_3
#define BIN1_GPIO_Port GPIOH
#define BIN2_Pin GPIO_PIN_8
#define BIN2_GPIO_Port GPIOB
#define PWMB_Pin GPIO_PIN_9
#define PWMB_GPIO_Port GPIOB

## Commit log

2025-02-06 modification README et ajout des répertoires
2025-02-06 ajout projet Kicad
    [PCB_Projet_1A.kicad_pcb, PCB_Projet_1A.kicad_sch]
2025-02-06 modification schematique
    [MCU_REGU.kicad_sch, PCB_Projet_1A.kicad_sch]
2025-02-06 finalisation schématique PCB
    [PCB_Projet_1A.kicad_pcb, PCB_Projet_1A.kicad_sch]
2025-02-06 Avancement sur le PCB editor
    [MCU_REGU.kicad_sch, PCB_Projet_1A.kicad_pcb, PCB_Projet_1A.kicad_sch]
2025-02-06 Finalisation du PCB et ajout du README dans le répertoire PCB
    [MCU_REGU.kicad_sch, PCB_Projet_1A.kicad_pcb, PCB_Projet_1A.kicad_sch]
2025-02-07 amélioration PCB : vias GND
    [PCB_Projet_1A.kicad_pcb]
2025-02-07 Update images du README PCB
2025-02-07 README PCB
2025-02-14 correction README HC05
    [PCB_Projet_1A.kicad_pcb]
2025-02-15 Modification du PCB: changement du HC05 SMD en pinheader adapté au module
    [PCB_Projet_1A.kicad_pcb, PCB_Projet_1A.kicad_sch]
2025-02-15 modification de F.silkscreen et B.silkscreen et du README PCB
    [PCB_Projet_1A.kicad_pcb]
2025-03-06 2eme modification de README Application
2025-04-03 modif pcb
    [MCU_REGU.kicad_sch, PCB_Projet_1A.kicad_pcb, PCB_Projet_1A.kicad_sch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]
2025-04-03 finalisation PCB v2
    [PCB_projetV2.kicad_pcb, PCB_projetV2.kicad_sch]
2025-04-03 ajout des screen shots du PCB v2 dans le répertoire PCB
2025-04-03 ajout des condensateurs pour les modules
    [PCB_projetV2.kicad_pcb, PCB_projetV2.kicad_sch]
2025-04-03 amélioration finale PCB
    [PCB_projetV2.kicad_pcb]
2025-04-03 ajour gerber PCBv2
    [PCB_projetV2-B_Cu.gbl, PCB_projetV2-B_Mask.gbs, PCB_projetV2-B_Paste.gbp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]
2025-04-10 MAJ PCB
    [PCB_projetV2.kicad_pcb]
2025-04-10 MAJ dossier PCB_v2
    [MCU_REGU.kicad_sch, PCB_Projet_1A.kicad_pcb, PCB_Projet_1A.kicad_sch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]
2025-04-10 ajout répertoire 3D
    [Modele3D_FusionAutodesk.f3d, Modele3D_Projet1A.stl]
2025-04-21 MAJ PCBv2
2025-05-31 Ajout de la derniere version du programme

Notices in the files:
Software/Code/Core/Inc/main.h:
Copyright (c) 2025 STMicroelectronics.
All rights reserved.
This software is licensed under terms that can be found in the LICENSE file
